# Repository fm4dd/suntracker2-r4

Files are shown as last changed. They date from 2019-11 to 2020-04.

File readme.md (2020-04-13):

# SunTracker2 Revision 4



This project is a photovoltaic (PV) solar tracking controller.

## Project

The design target is a self-orienting dual-axis, scheduled, Arduino-based solar
tracker model, demonstrating PV panel orientation for both Elevation and
Azimuth angles (dual-axis). The Sun orientation is achieved through pre-calculated
solar position data for a specific geographic location and time (scheduled).

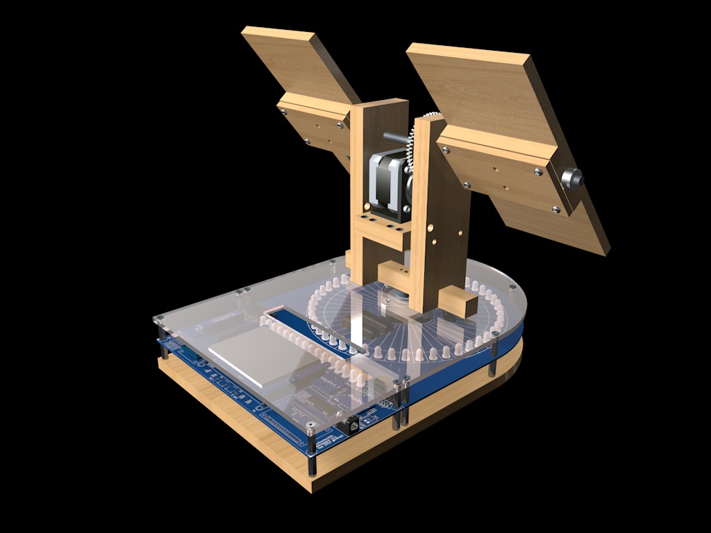
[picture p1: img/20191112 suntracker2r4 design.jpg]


Working under space, cost and time constraints, this prototype model is the
follow-up project to SunTracker2 Revision 3.

## Functional Design

In order to clearly understand, demonstrate and validate the sun tracking function,
a 48 dual-color LED ring represents the horizon with north, sunrise and sunset
indicators. A green indicator displays the suns daily movement over time.
Two NEMA stepper motors align the solar panel model with the sun.

### Board Components

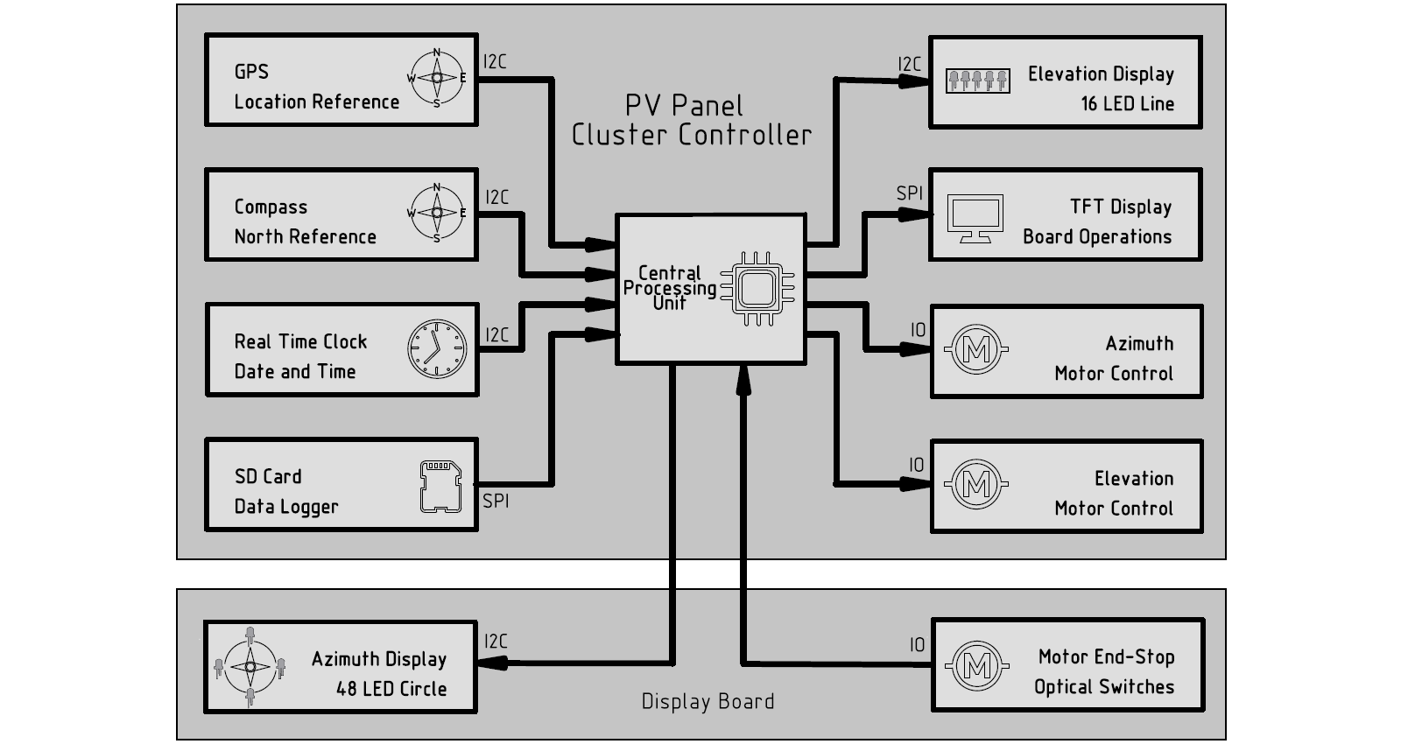
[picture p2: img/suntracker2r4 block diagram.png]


### Mainboard, PCB

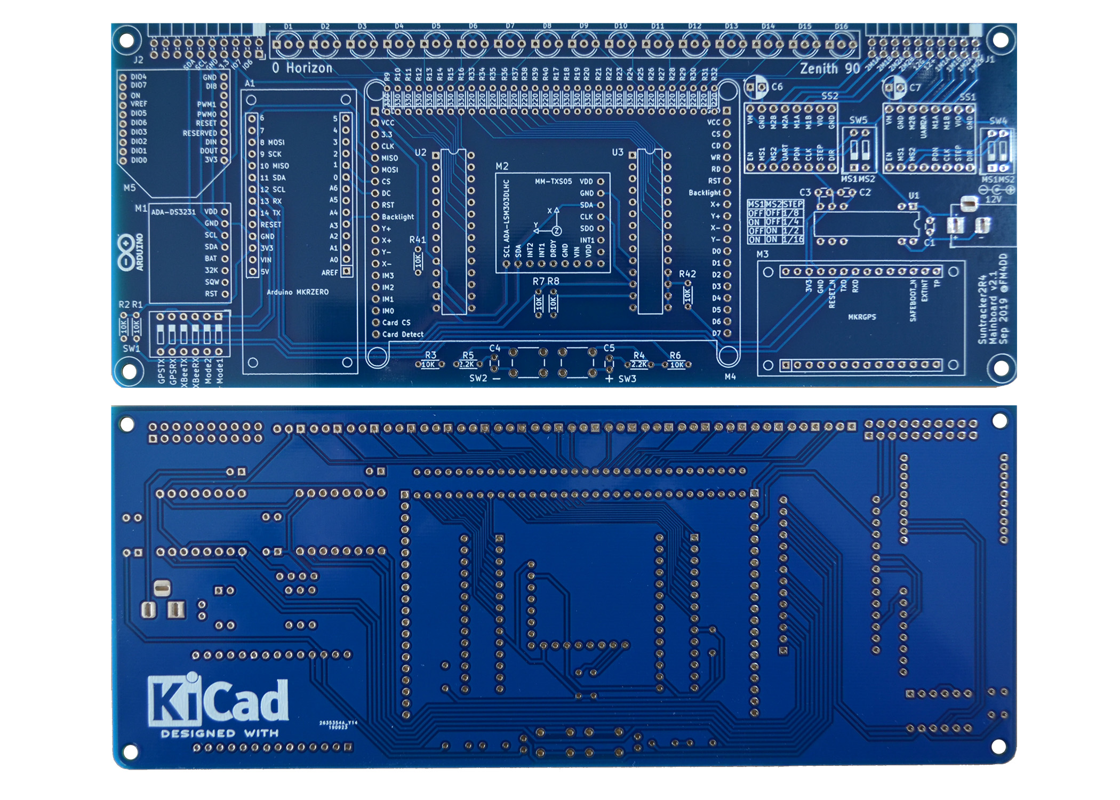
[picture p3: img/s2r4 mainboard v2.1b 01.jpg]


### Mainboard PCB, bottom layer 

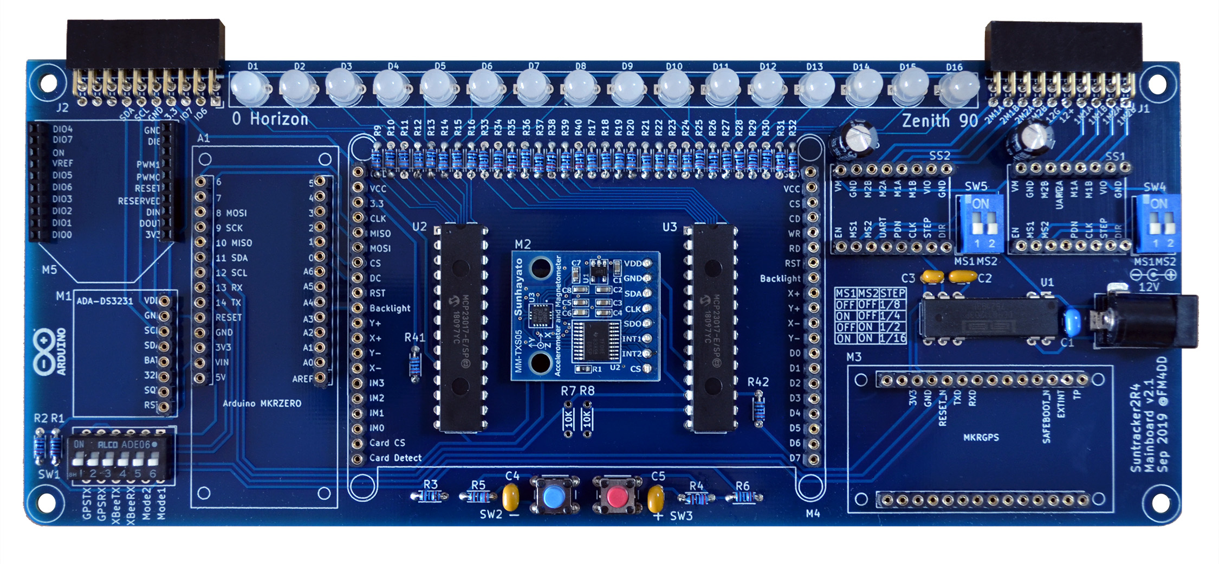
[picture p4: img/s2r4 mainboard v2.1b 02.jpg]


### Mainboard, fully populated

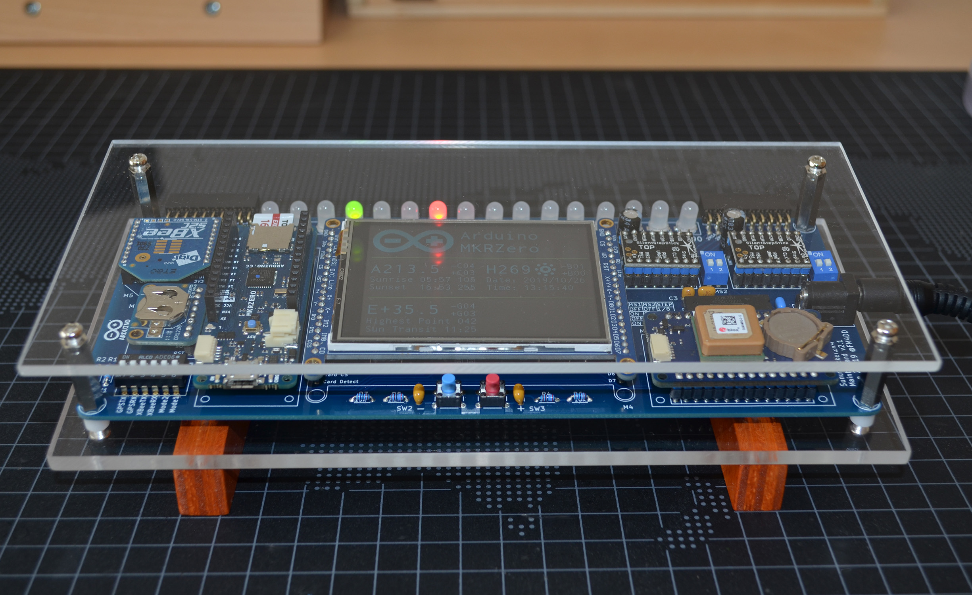
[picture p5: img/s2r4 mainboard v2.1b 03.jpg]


### Mainboard, TFT display layout

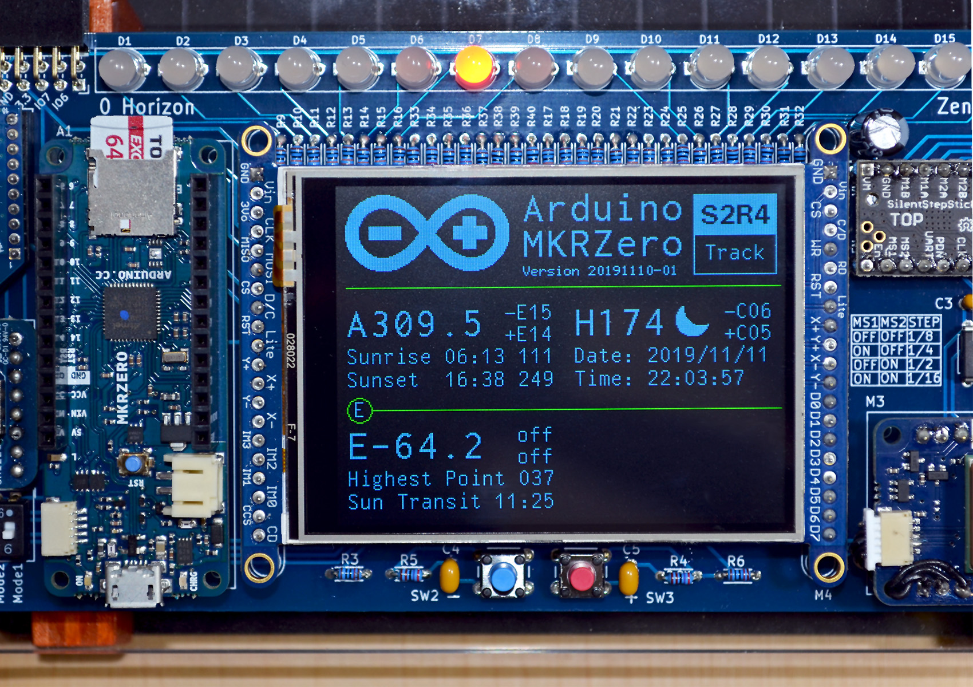
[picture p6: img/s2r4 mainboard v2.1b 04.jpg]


### Displayboard, PCB

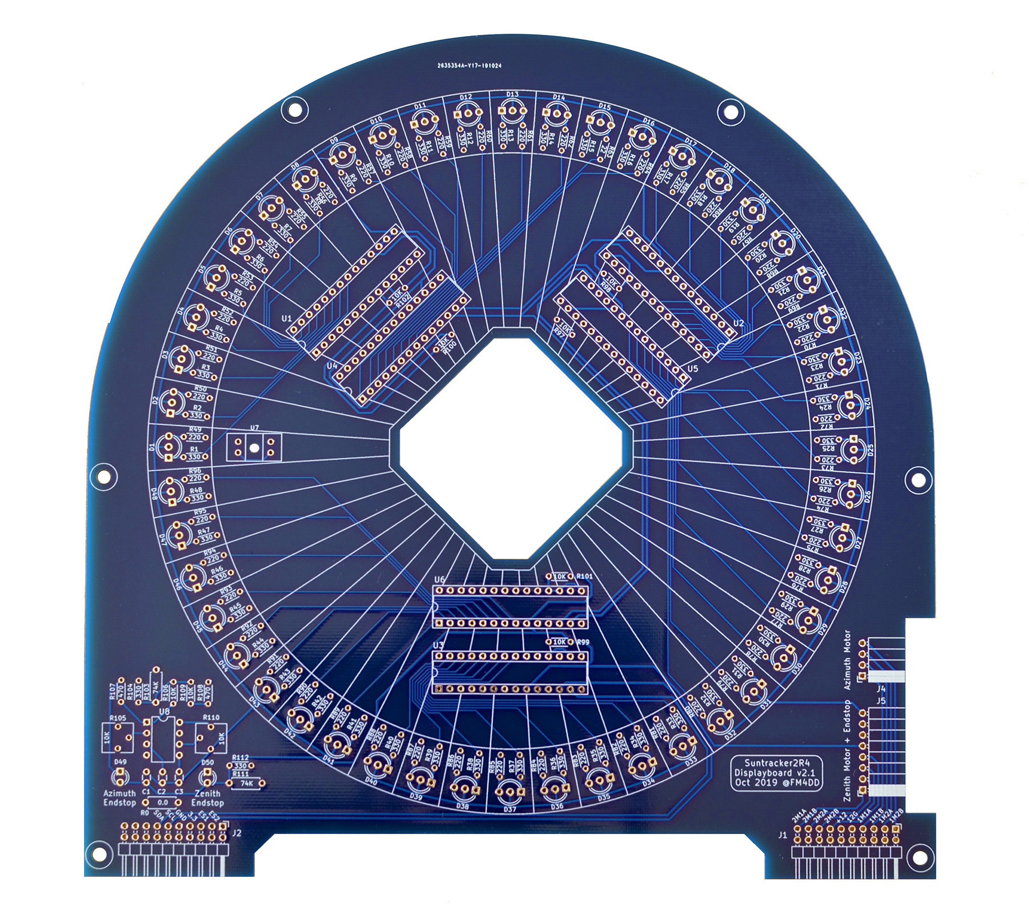
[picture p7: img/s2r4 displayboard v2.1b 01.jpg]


### Displayboard, IO Expander close-up

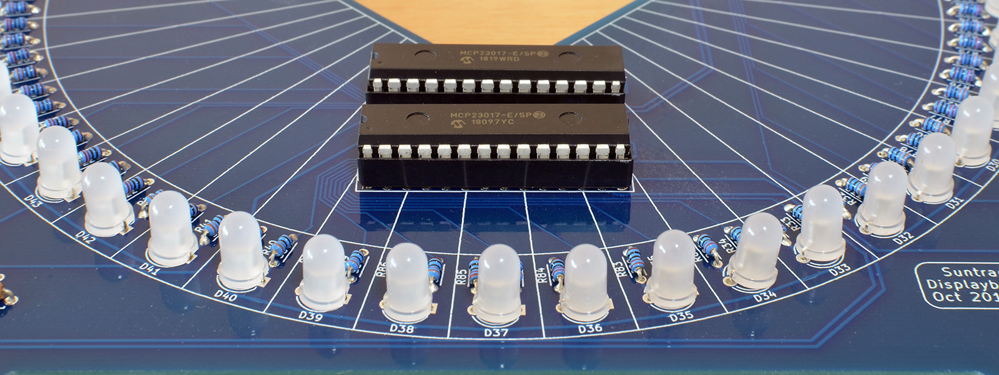
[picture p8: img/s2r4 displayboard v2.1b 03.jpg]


### Mainboard and Displayboard connected

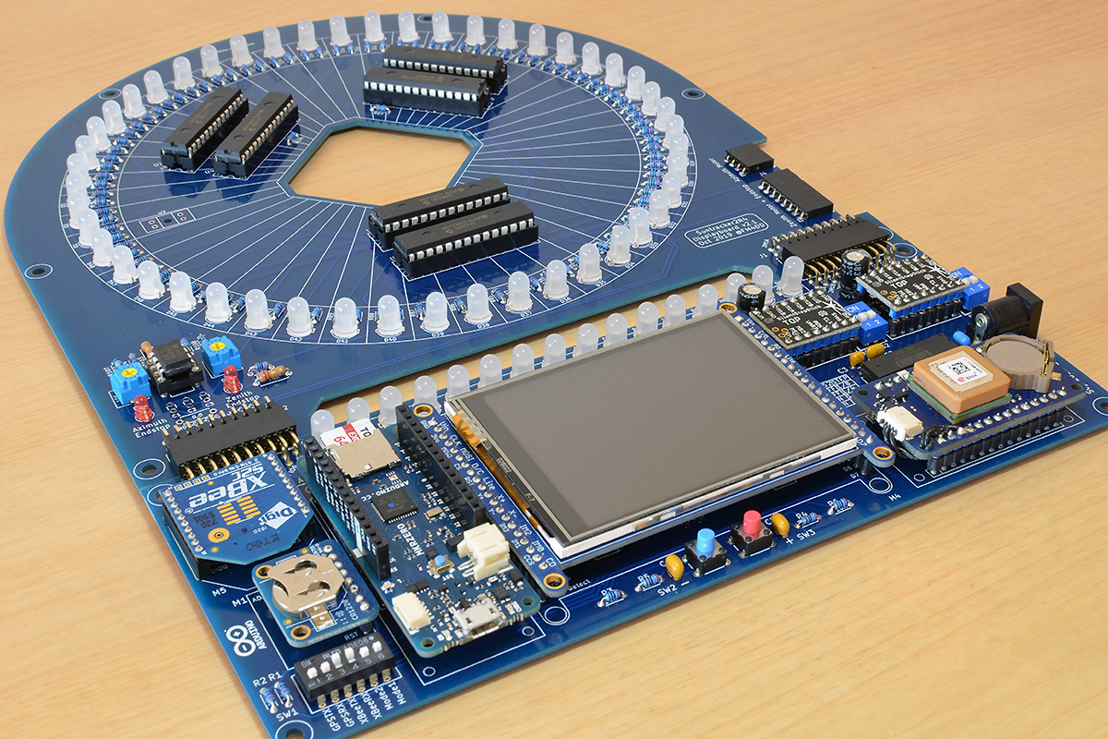
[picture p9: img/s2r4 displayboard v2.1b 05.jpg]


### Device Assembly

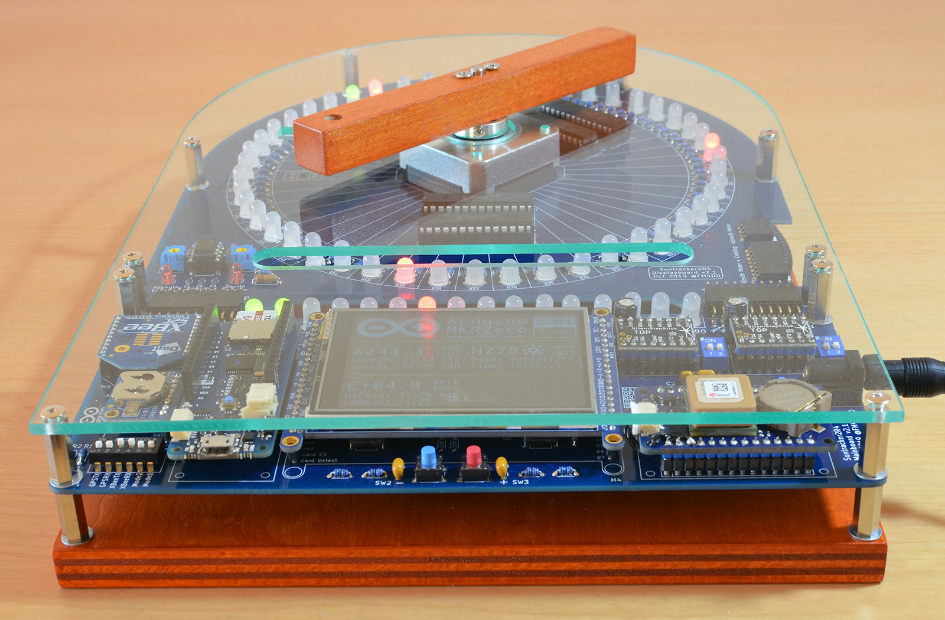
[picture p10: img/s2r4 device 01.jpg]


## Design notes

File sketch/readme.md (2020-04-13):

# mainboard-rev4 sketch compilation



```
Sketch uses 100056 bytes (38%) of program storage space. Maximum is 262144 bytes.
Global variables use 16600 bytes of dynamic memory.
Atmel SMART device 0x10010005 found
Device       : ATSAMD21G18A
Chip ID      : 10010005
Version      : v2.0 [Arduino:XYZ] Dec 20 2016 15:36:46
Address      : 8192
Pages        : 3968
Page Size    : 64 bytes
Total Size   : 248KB
Planes       : 1
Lock Regions : 16
Locked       : none
Security     : false
Boot Flash   : true
BOD          : true
BOR          : true
Arduino      : FAST_CHIP_ERASE
Arduino      : FAST_MULTI_PAGE_WRITE
Arduino      : CAN_CHECKSUM_MEMORY_BUFFER
Erase flash
done in 0.844 seconds

Write 100056 bytes to flash (1564 pages)

[=                             ] 4% (64/1564 pages)
[==                            ] 8% (128/1564 pages)
[===                           ] 12% (192/1564 pages)
[====                          ] 16% (256/1564 pages)
[======                        ] 20% (320/1564 pages)
[=======                       ] 24% (384/1564 pages)
[========                      ] 28% (448/1564 pages)
[=========                     ] 32% (512/1564 pages)
[===========                   ] 36% (576/1564 pages)
[============                  ] 40% (640/1564 pages)
[=============                 ] 45% (704/1564 pages)
[==============                ] 49% (768/1564 pages)
[===============               ] 53% (832/1564 pages)
[=================             ] 57% (896/1564 pages)
[==================            ] 61% (960/1564 pages)
[===================           ] 65% (1024/1564 pages)
[====================          ] 69% (1088/1564 pages)
[======================        ] 73% (1152/1564 pages)
[=======================       ] 77% (1216/1564 pages)
[========================      ] 81% (1280/1564 pages)
[=========================     ] 85% (1344/1564 pages)
[===========================   ] 90% (1408/1564 pages)
[============================  ] 94% (1472/1564 pages)
[============================= ] 98% (1536/1564 pages)
[==============================] 100% (1564/1564 pages)
done in 0.723 seconds

Verify 100056 bytes of flash with checksum.
Verify successful
done in 0.090 seconds
CPU reset.
```

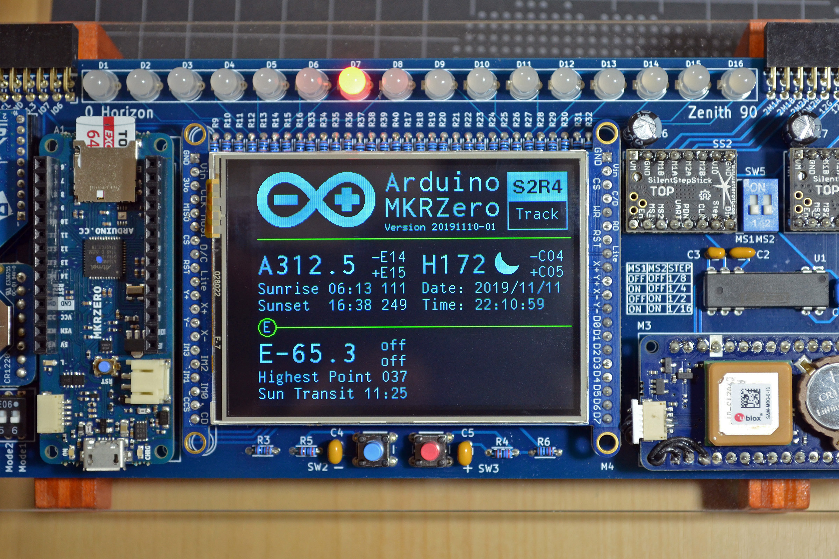
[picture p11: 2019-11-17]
img/s2r4 mainboard v2.1b 05.jpg

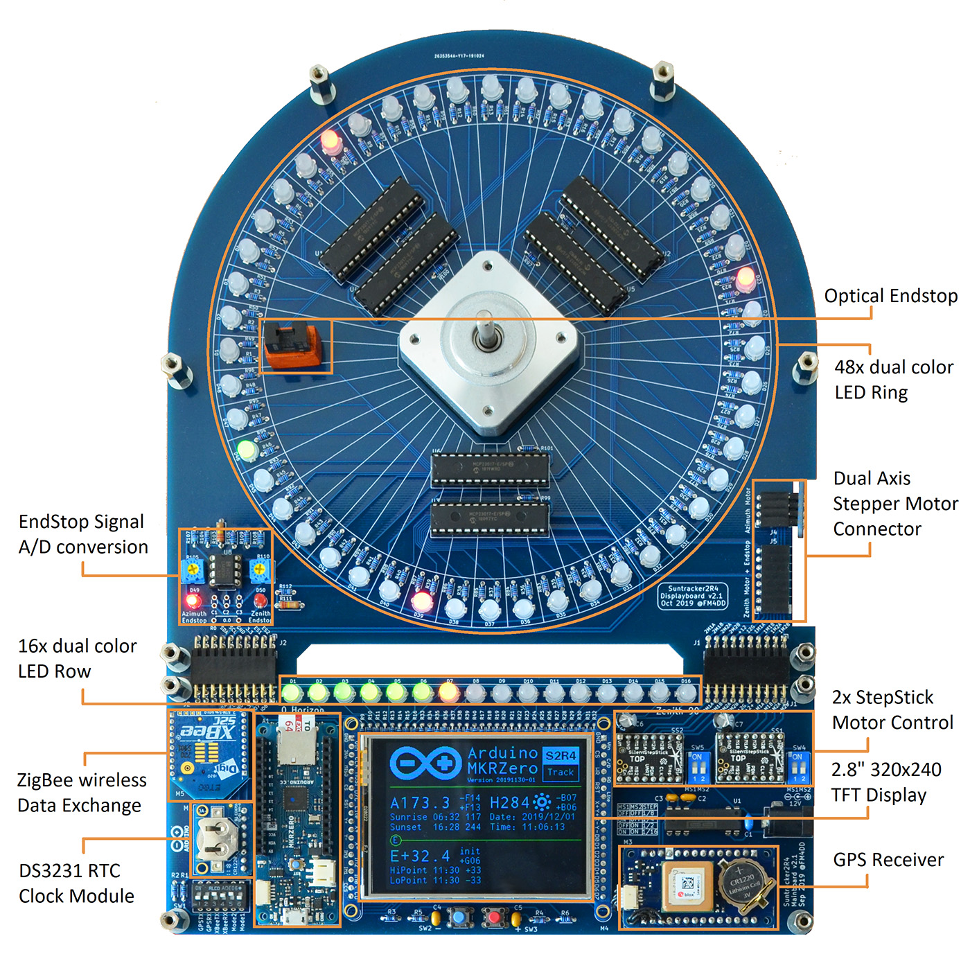
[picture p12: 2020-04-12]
img/s2r4 description.jpg

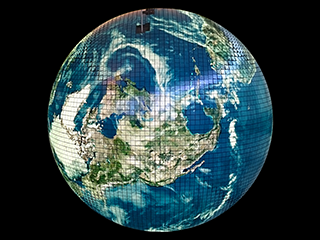
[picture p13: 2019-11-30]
sketch/mainboard-rev4/s2r4img.bmp

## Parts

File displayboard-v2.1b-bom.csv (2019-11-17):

Manufacturer Part Number | Manufacturer | Digi-Key Part Number | Customer Reference | Quantity | Description
K104K15X7RF5TL2 | Vishay BC Components | BC1084CT-ND | C1,C2,C3 | 3 | CAP CER 0.1UF 50V X7R RADIAL
CD14ZT0R00 | Stackpole Electronics Inc | CD14ZT0R00CT-ND | R0 | 1 | RES 0 OHM 1/4W JUMP AXIAL
RNMF14FTC330R | Stackpole Electronics Inc | S330CACT-ND | R1-48,R104,R112 | 50 | RES 330 OHM 1/4W 1% AXIAL
RNMF14FTC470R | Stackpole Electronics Inc | S470CACT-ND | R107,R108 | 2 | RES 470 OHM 1/4W 1% AXIAL
RNMF14FTC220R | Stackpole Electronics Inc | S220CACT-ND | R49-96 | 48 | RES 220 OHM 1/4W 1% AXIAL
RNMF14FTC10K0 | Stackpole Electronics Inc | S10KCACT-ND | R97-R102 | 6 | RES 10K OHM 1/4W 1% AXIAL
PEC10DBAN | Sullins Connector Solutions | S2112E-10-ND | J1,J2 | 2 | CONN HEADER R/A 20POS 2.54MM
PPPC041LGBN-RC | Sullins Connector Solutions | S5479-ND | J4 | 1 | CONN HDR 4POS 0.1 GOLD PCB R/A
PPPC081LGBN-RC | Sullins Connector Solutions | S5483-ND | J5 | 1 | CONN HDR 8POS 0.1 GOLD PCB R/A
ROB-09238 | SparkFun Electronics | 1568-1105-ND | M1,M2 | 2 | STEPPER MOTOR HYBRID BIPOLAR 12V
LTL-30EHJ | Lite-On Inc. | 160-1057-ND | D1-D48 | 48 | LED GRN/RED DIFFUSED T-1 3/4 T/H
151031SS04000 | Wurth Electronics Inc. | 732-5005-ND | D49,D50 | 2 | LED RED DIFFUSED 3MM ROUND T/H
ED281DT | On Shore Technology Inc. | ED3050-5-ND | U1-U6 | 6 | CONN IC DIP SOCKET 28POS TIN
MCP23017-E/SP | Microchip Technology | MCP23017-E/SP-ND | U1-U6 | 6 | IC I/O EXPANDER I2C 16B 28SDIP
OPB804 | TT Electronics/Optek Technology | 365-1017-ND | U7,U9 | 2 | OPB804 SENSOR OPT SLOT PHOTOTRAN PCB MT
LM393P | Texas Instruments | 296-1398-5-ND | U8 | 1 | LM393 IC DUAL DIFF COMP 8-DIP

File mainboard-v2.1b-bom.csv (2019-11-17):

Manufacturer Part Number | Manufacturer | Digi-Key Part Number | Customer Reference | Quantity | Description
ABX00012 | Arduino | 1050-1137-ND | A1 | 1 | ARDUINO MKR ZERO W/ HDR ATSAMD21
ASX00017 | Arduino | 1050-1171-ND | M3 | 1 | ARDUINO MKR GPS SHIELD
MCP23017-E/SP | Microchip Technology | MCP23017-E/SP-ND | U1,U2 | 2 | IC I/O EXPANDER I2C 16B 28SDIP
1770 | Adafruit Industries LLC | 1528-1469-ND | M4 | 1 | 2.8" TFT LCD TOUCHSCREEN
1120 | Adafruit Industries LLC | 1528-1173-ND | M2 | 1 | BOARD ACCEL/COMPASS 3AXIS LSM303
3013 | Adafruit Industries LLC | 1528-1598-ND | M1 | 1 | ADAFRUIT DS3231 PRECISION RTC BR
TMC2208 SILENTSTEPSTICK | Trinamic Motion Control GmbH | 1460-1201-ND | SS1,SS2 | 2 | TMC2208 STEPPER DRIVER BOARD
1825057-1 | TE Connectivity ALCOSWITCH Switches | 450-1363-ND | SWI4,SWI5 | 2 | SWITCH SLIDE DIP SPST 100MA 24V
1825360-4 | TE Connectivity ALCOSWITCH Switches | 450-3353-ND | SWI1 | 1 | SWITCH SLIDE DIP SPST 100MA 24V
151031SS04000 | Wurth Electronics Inc. | 732-5005-ND | D1,D2,D3,D4 | 4 | LED RED DIFFUSED 3MM ROUND T/H
C320C105K5N5TA91707301 | KEMET | 399-14394-1-ND | C1,C2 | 2 | CAP CER 1UF 50V X8L RADIAL
DCR011203P | Texas Instruments | 296-36927-5-ND | U1 | 1 | DC DC CONVERTER 3.3V 1W
476CKE035M | Illinois Capacitor | 1572-1473-ND | C6,C7 | 2 | CAP ALUM 47UF 20% 35V RADIAL
PPTC102LJBN-RC | Sullins Connector Solutions | S5524-ND | J1,J2 | 2 | CONN HDR 20POS 0.1 TIN PCB R/A
SMC-1-40-1-GT | Adam Tech | 2057-SMC-1-40-1-GT-ND | Circuit Sockets | 2 | MACHINE PIN SOCKET 40P 1.00MM PI
1825910-6 | TE Connectivity ALCOSWITCH Switches | 450-1650-ND | SWI2,SWI3 | 2 | SWITCH TACTILE SPST-NO 0.05A 24V
RNMF14FTC10K0 | Stackpole Electronics Inc | S10KCACT-ND | R1,R2,R5,R6,R9,R10,R11,R12,R13,R14 | 10 | RES 10K OHM 1/4W 1% AXIAL
RNMF14FTC330R | Stackpole Electronics Inc | S330CACT-ND | R3,R4,R7,R8 | 16 | RES 330 OHM 1/4W 1% AXIAL
RNMF14FTC220R | Stackpole Electronics Inc | S220CACT-ND | R3,R4,R7,R8 | 16 | RES 220 OHM 1/4W 1% AXIAL
RNMF14FTC2K20 | Stackpole Electronics Inc | S2.2KCACT-ND | R15,R16 | 2 | RES 2.2K OHM 1/4W 1% AXIAL
PJ-002A | CUI Inc. | CP-002A-ND | 12V Barrel Jack | 1 | CONN PWR JACK 2X5.5MM SOLDER
LTL-30EHJ | Lite-On Inc. | 160-1057-ND | D1-D16 | 16 | LED GRN/RED DIFFUSED T-1 3/4 T/H
XB24CZ7PIT-004 | Digi International | 602-1557-ND | M5 | 1 | RF TXRX MOD 802.15.4 TRACE ANT

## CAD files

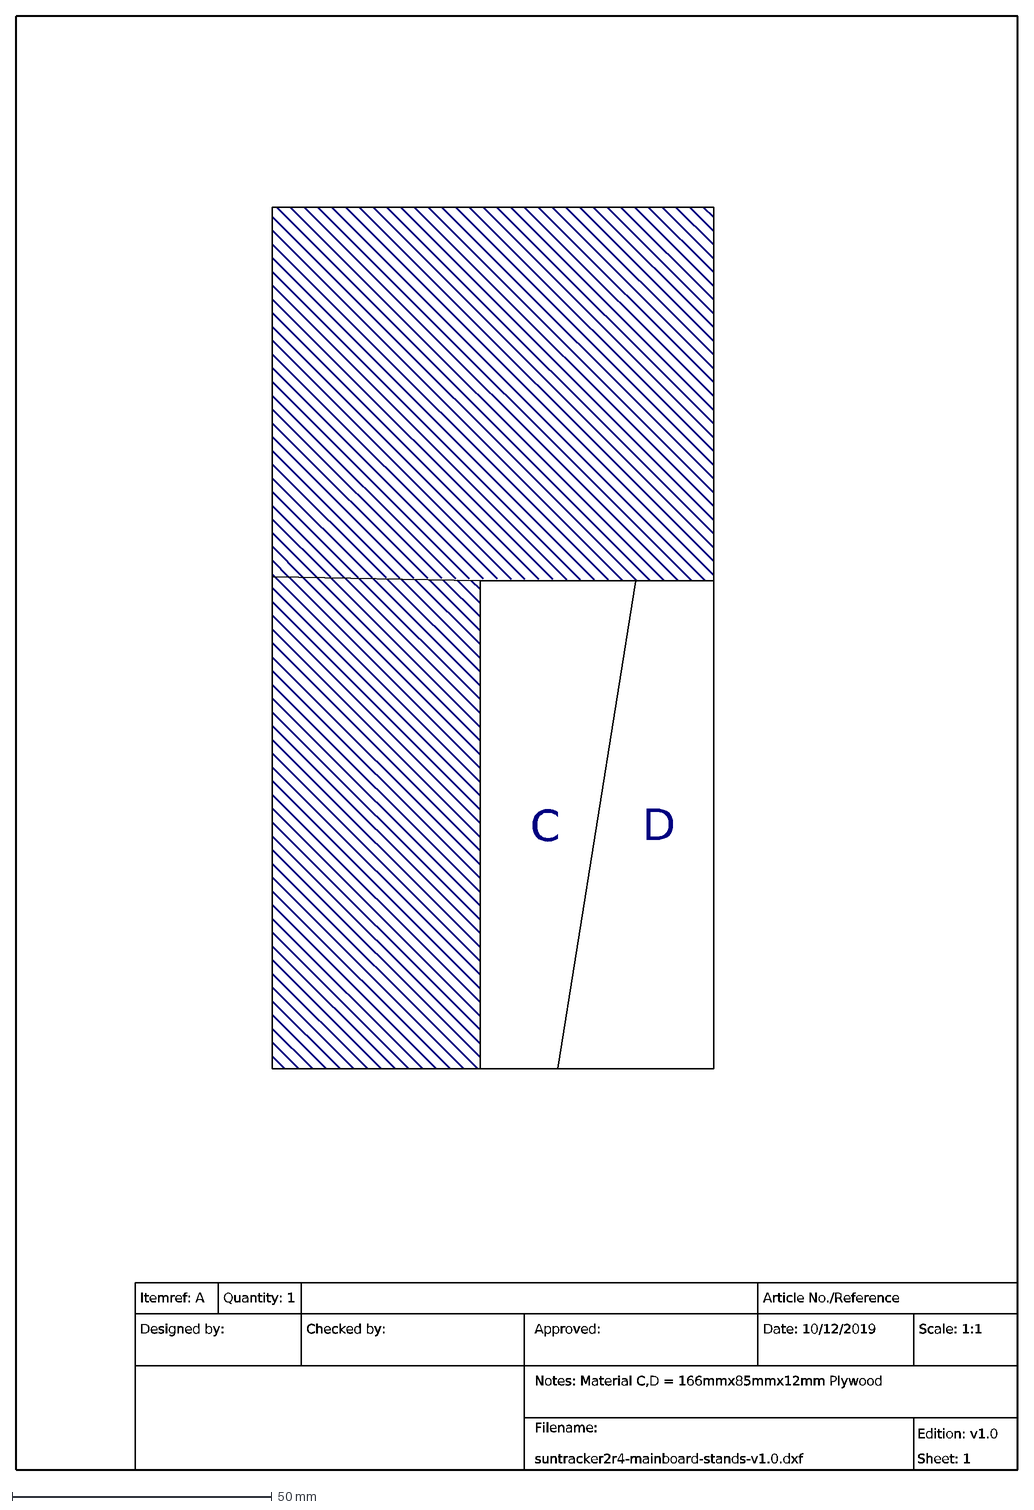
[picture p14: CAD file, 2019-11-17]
cad/20191012 suntracker2r4-mainboard-stands-v1.0.dxf
Notes: Material C,D = 166mmx85mmx12mm Plywood
Itemref: A
Quantity: 1
Article No./Reference
Designed by:
Checked by:
Approved:
Filename: suntracker2r4-mainboard-stands-v1.0.dxf
Date: 10/12/2019
Scale: 1:1
Edition: v1.0 Sheet: 1
C
D

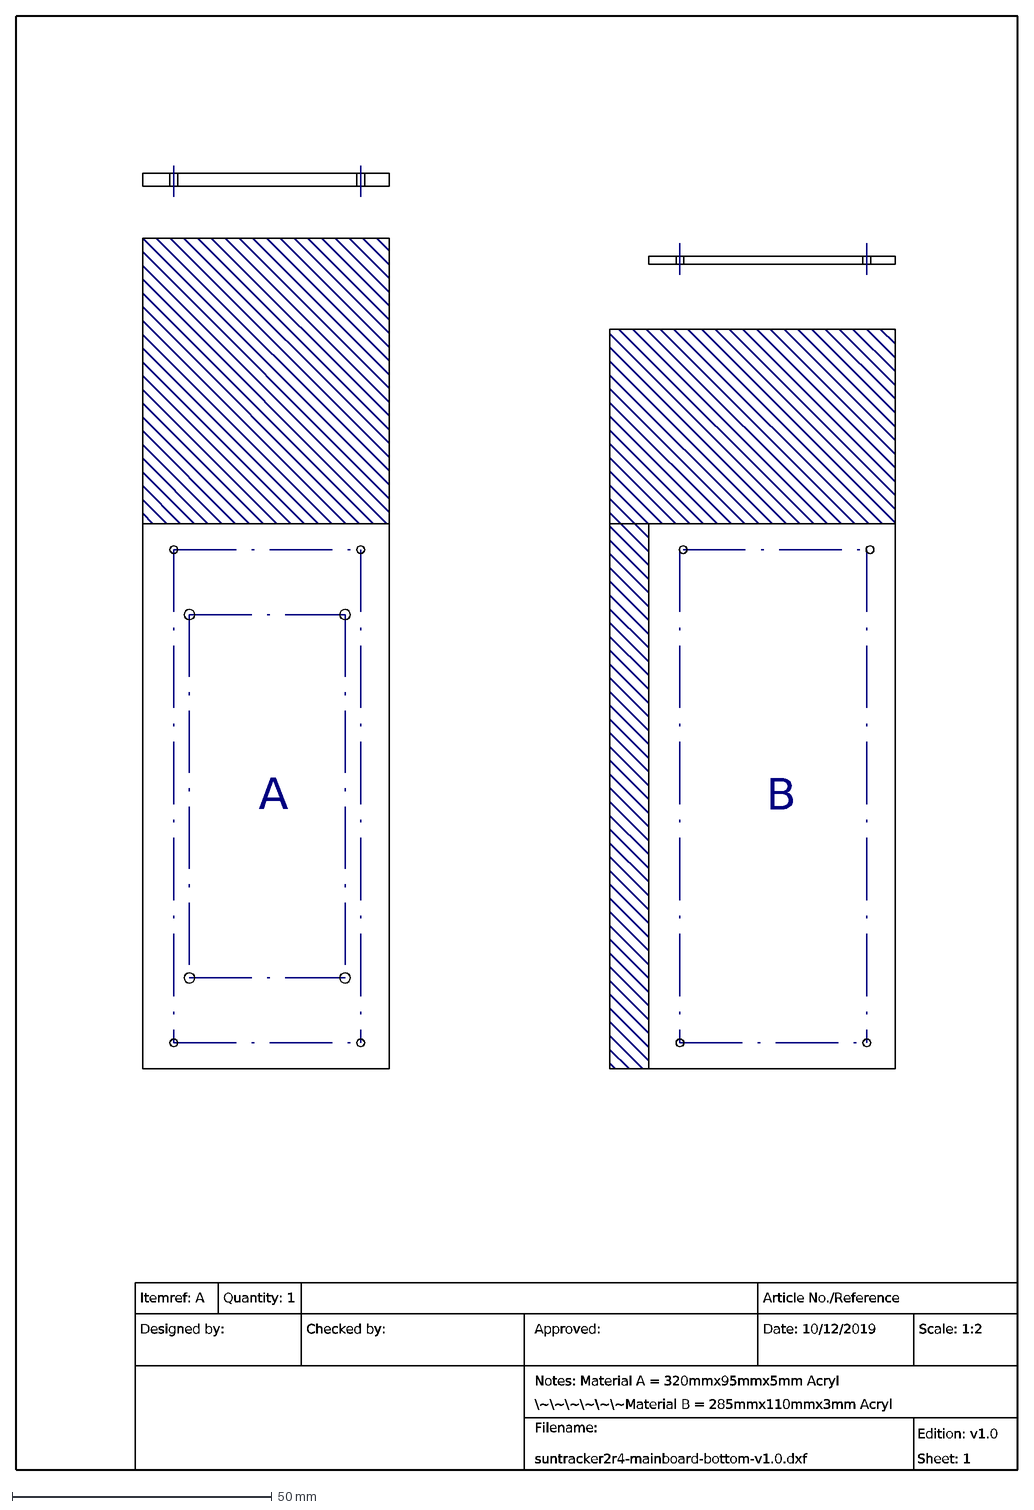
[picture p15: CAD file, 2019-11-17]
cad/20191012 suntracker2r4-mainboard-bottom-v1.0.dxf
Notes: Material A = 320mmx95mmx5mm Acryl \~\~\~\~\~\~Material B = 285mmx110mmx3mm Acryl
Itemref: A
Quantity: 1
Article No./Reference
Designed by:
Checked by:
Approved:
Filename: suntracker2r4-mainboard-bottom-v1.0.dxf
Date: 10/12/2019
Scale: 1:2
Edition: v1.0 Sheet: 1
A
B

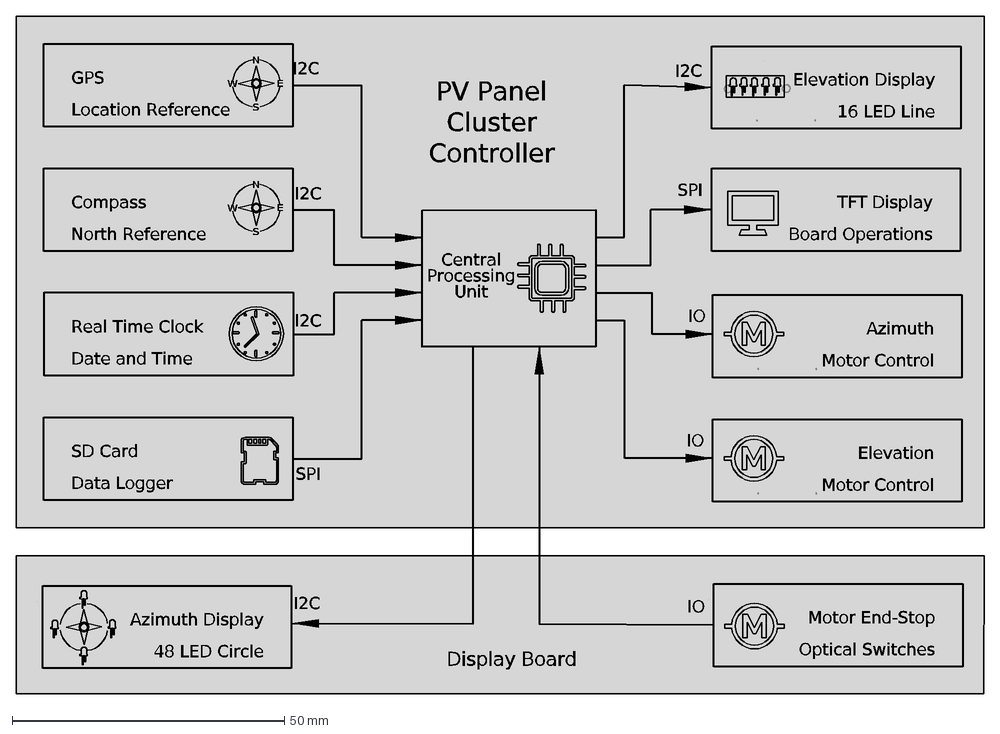
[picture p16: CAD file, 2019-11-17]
cad/20190922 Suntracker2r4 block diagram.dxf
Compass North Reference
GPS Location Reference
Real Time Clock Date and Time
Azimuth Display 48 LED Circle
Motor End-Stop Optical Switches
Elevation Display 16 LED Line
TFT Display Board Operations
SD Card Data Logger
Azimuth Motor Control
Elevation Motor Control
Central Processing Unit
S
W
E
N
SPI
I2C
IO
Display Board
PV Panel Cluster Controller

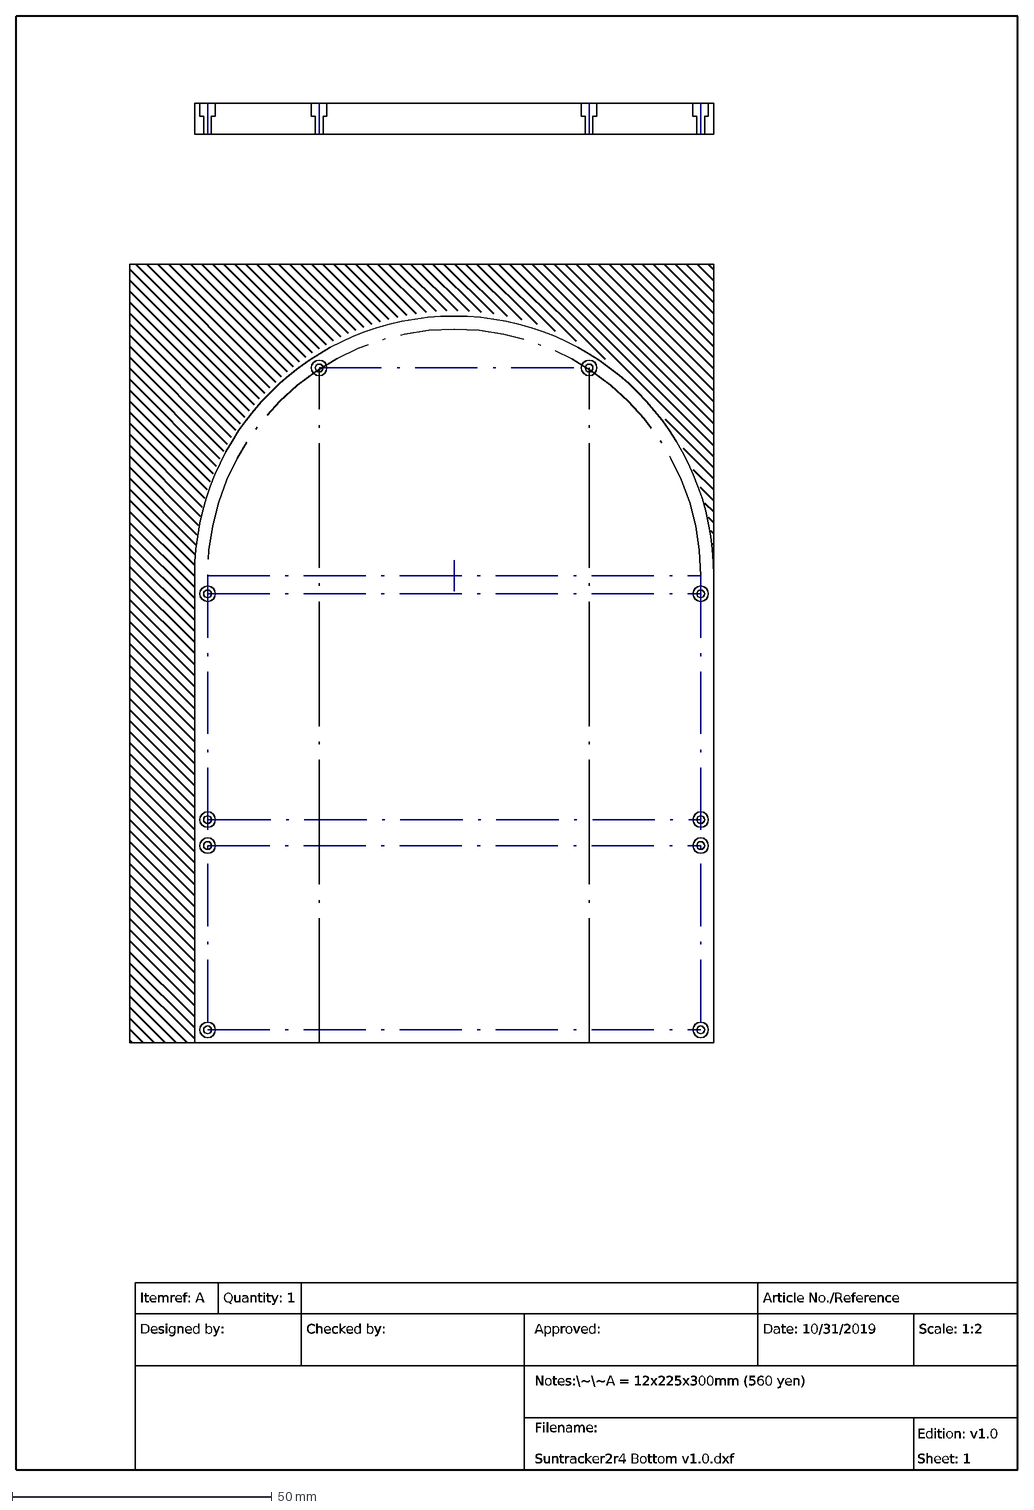
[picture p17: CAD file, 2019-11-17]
cad/20191031 Suntracker2r4 enclosure Bottom v1.0.dxf
Notes:\~\~A = 12x225x300mm (560 yen)
Itemref: A
Quantity: 1
Article No./Reference
Designed by:
Checked by:
Approved:
Filename: Suntracker2r4 Bottom v1.0.dxf
Date: 10/31/2019
Scale: 1:2
Edition: v1.0 Sheet: 1

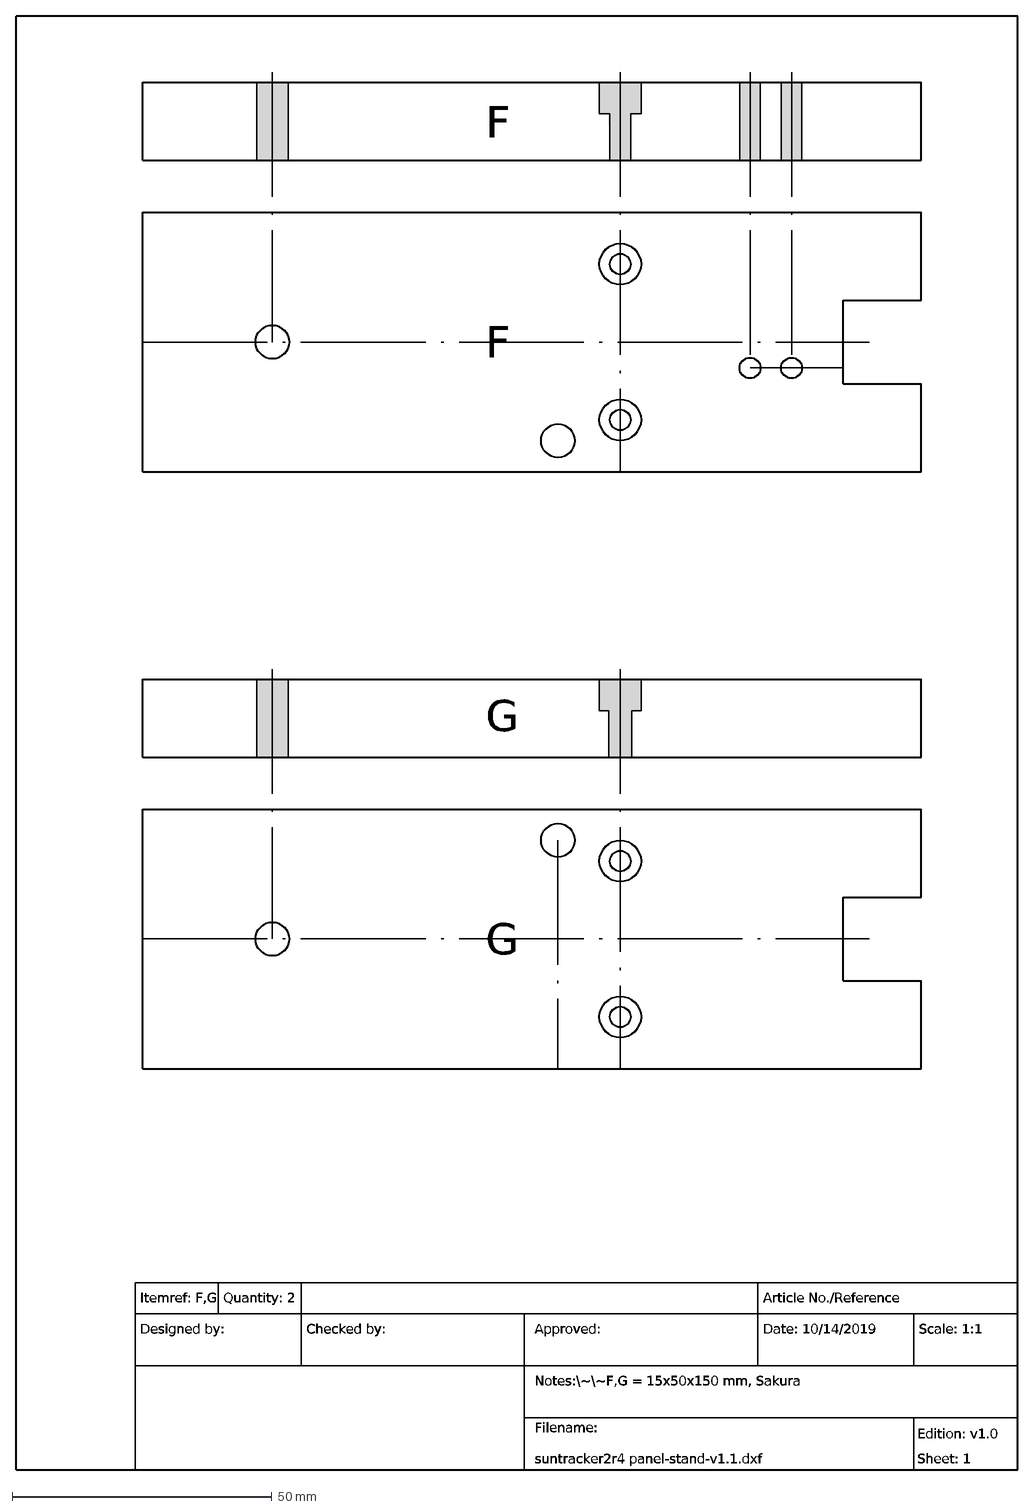
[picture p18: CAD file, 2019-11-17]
cad/20191014 Suntracker2r4 panel-stand-v1.1.dxf
Notes:\~\~F,G = 15x50x150 mm, Sakura
Itemref: F,G
F
G
Quantity: 2
Article No./Reference
Designed by:
Checked by:
Approved:
Filename: suntracker2r4 panel-stand-v1.1.dxf
Date: 10/14/2019
Scale: 1:1
Edition: v1.0 Sheet: 1

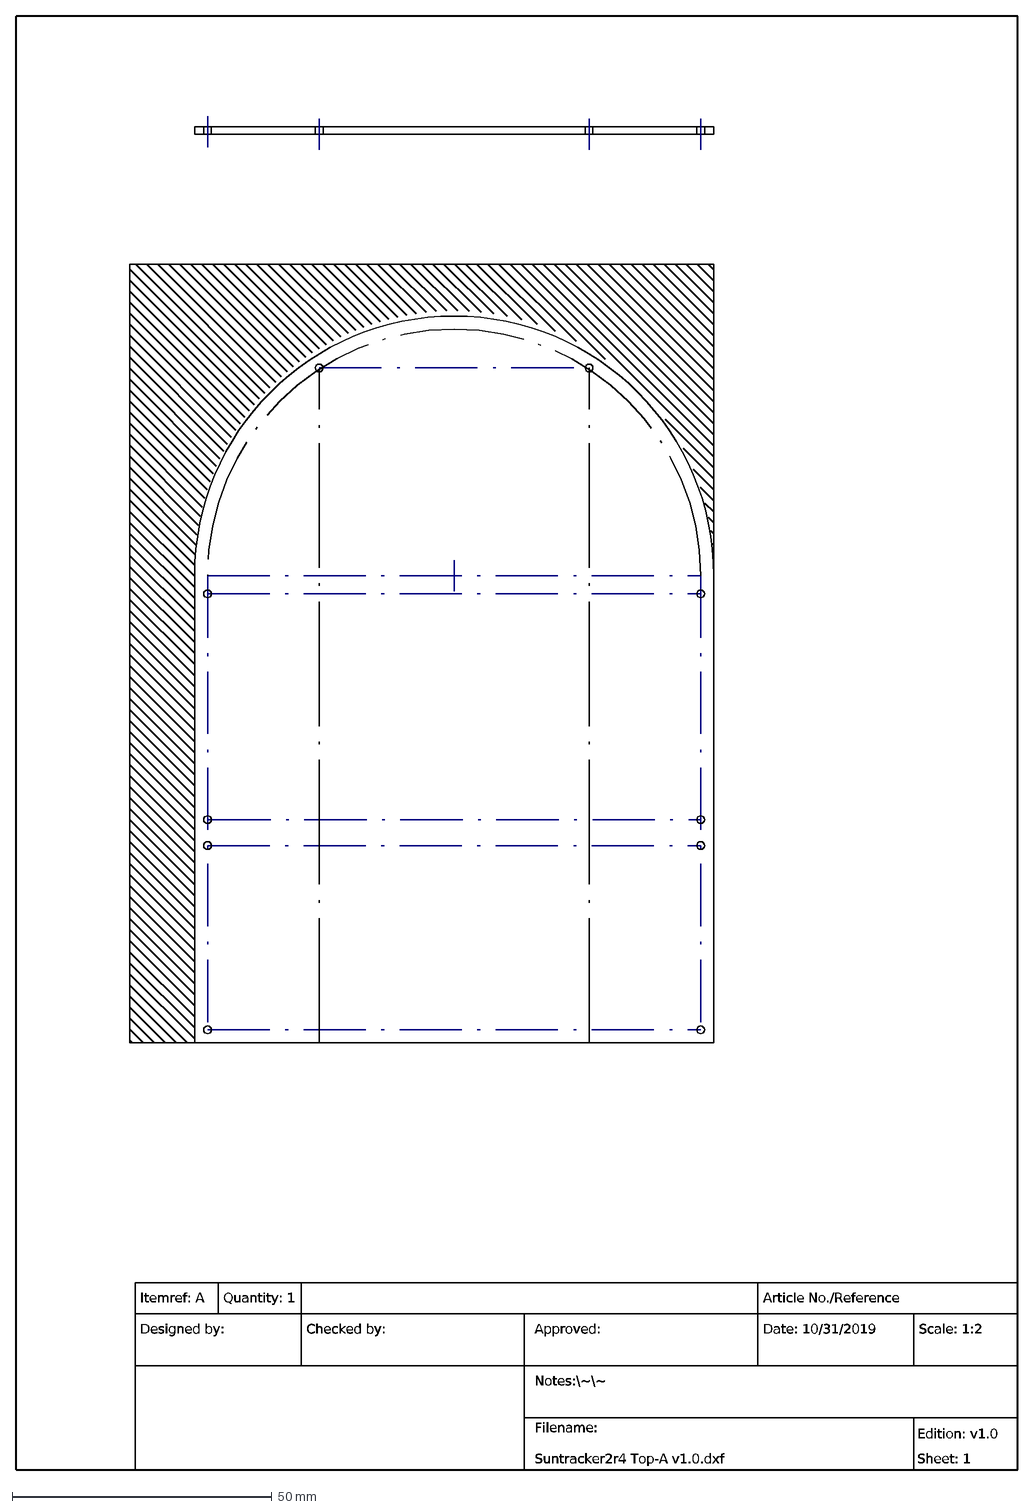
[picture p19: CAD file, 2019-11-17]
cad/20191031 Suntracker2r4 enclosure TopA v1.0.dxf
Notes:\~\~
Itemref: A
Quantity: 1
Article No./Reference
Designed by:
Checked by:
Approved:
Filename: Suntracker2r4 Top-A v1.0.dxf
Date: 10/31/2019
Scale: 1:2
Edition: v1.0 Sheet: 1

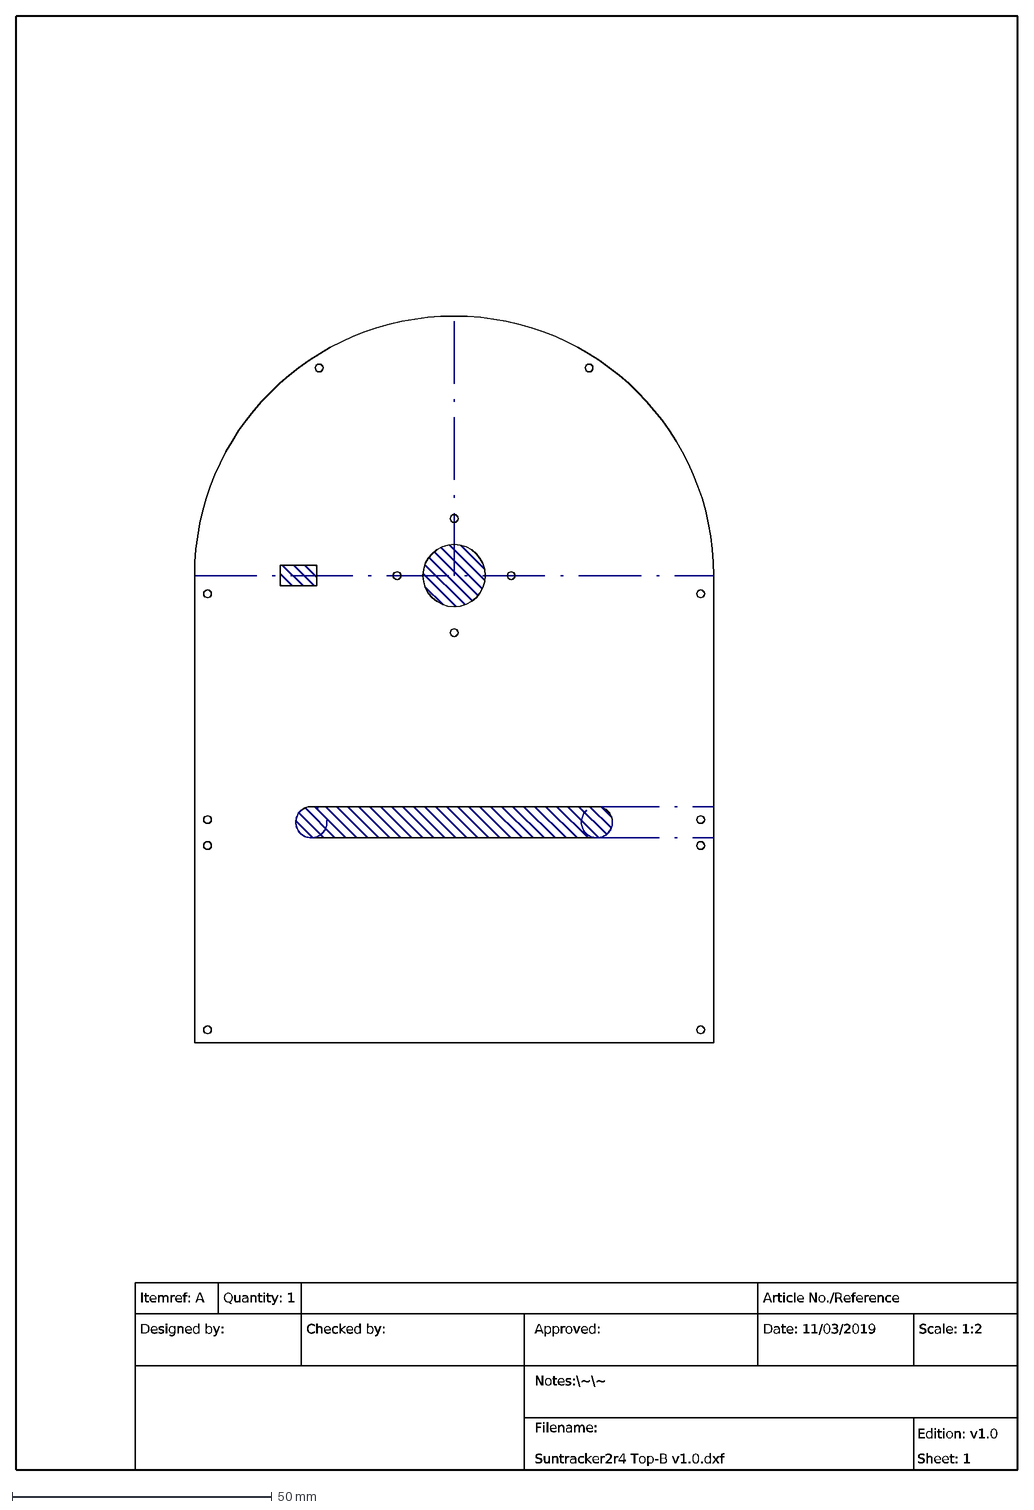
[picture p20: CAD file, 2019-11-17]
cad/20191031 Suntracker2r4 enclosure TopB v1.0.dxf
Notes:\~\~
Itemref: A
Quantity: 1
Article No./Reference
Designed by:
Checked by:
Approved:
Filename: Suntracker2r4 Top-B v1.0.dxf
Date: 11/03/2019
Scale: 1:2
Edition: v1.0 Sheet: 1

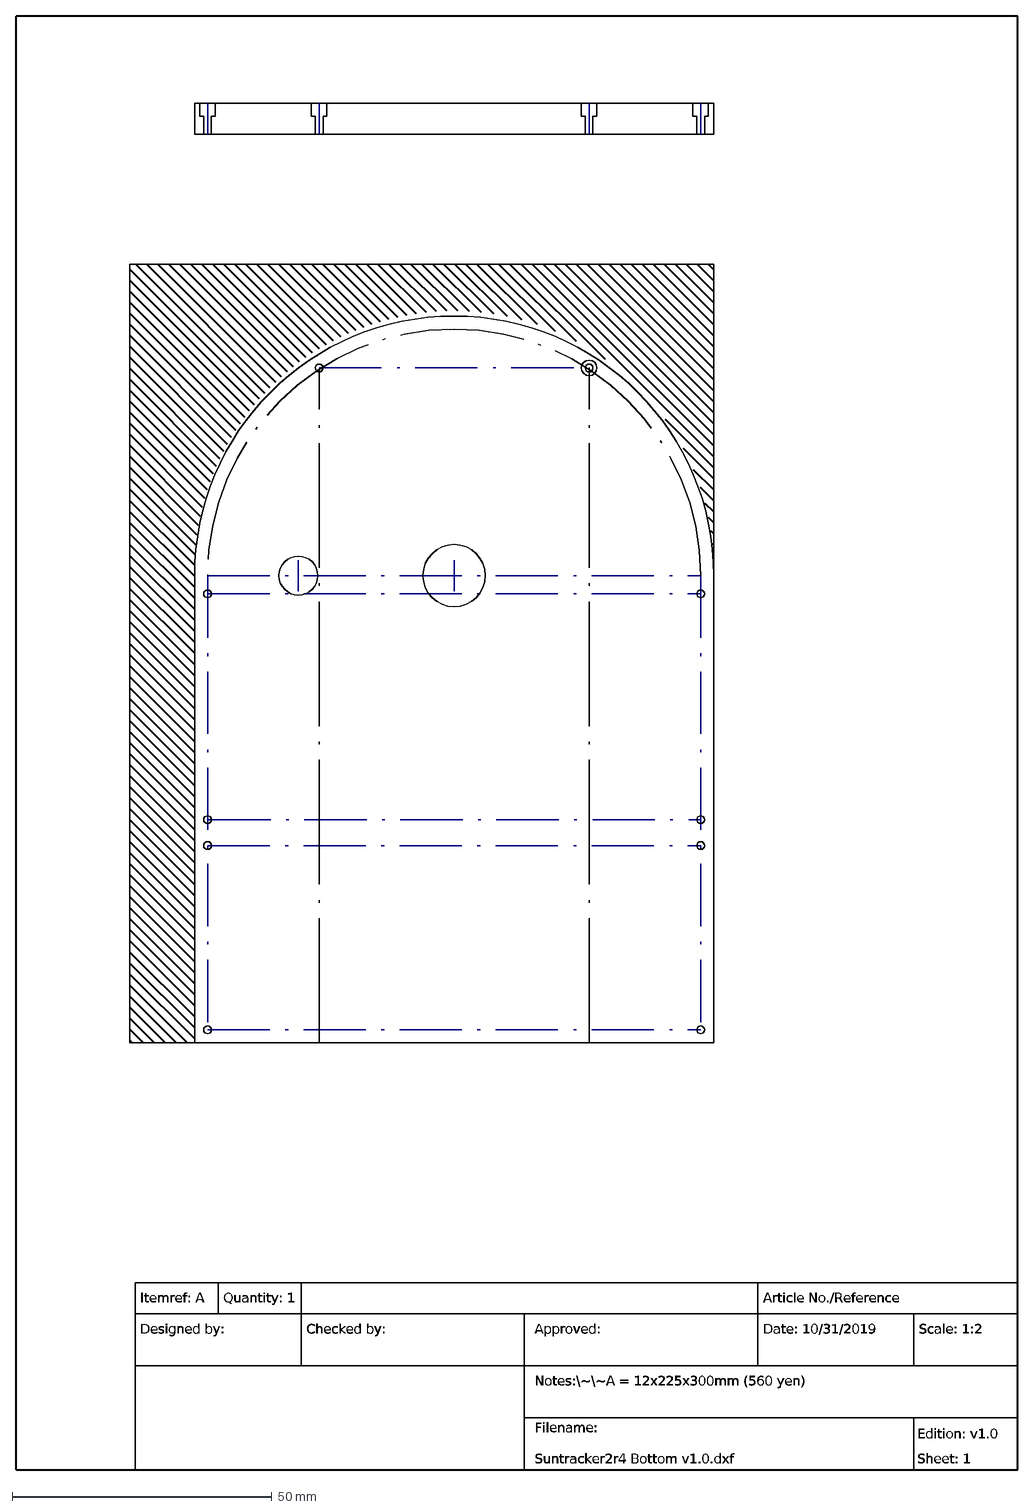
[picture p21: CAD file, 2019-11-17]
cad/20191031 Suntracker2r4 enclosure Top v1.0.dxf
Notes:\~\~A = 12x225x300mm (560 yen)
Itemref: A
Quantity: 1
Article No./Reference
Designed by:
Checked by:
Approved:
Filename: Suntracker2r4 Bottom v1.0.dxf
Date: 10/31/2019
Scale: 1:2
Edition: v1.0 Sheet: 1

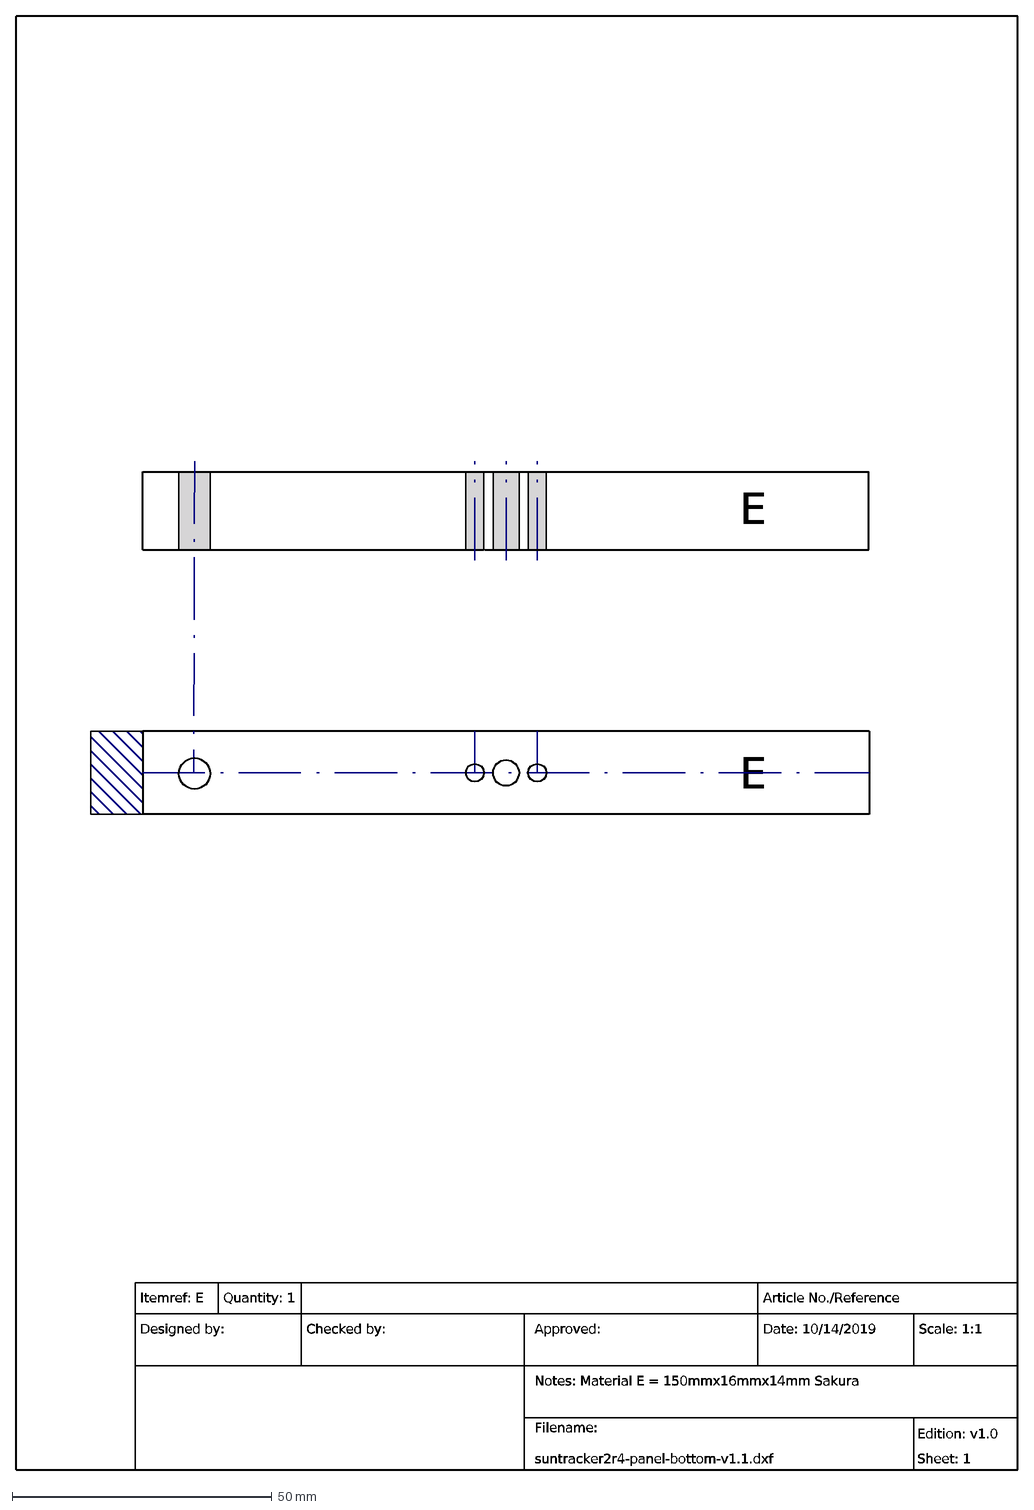
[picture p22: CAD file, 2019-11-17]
cad/20191014 suntracker2r4-panel-bottom-v1.1.dxf
Notes: Material E = 150mmx16mmx14mm Sakura
Itemref: E
Quantity: 1
Article No./Reference
Designed by:
Checked by:
Approved:
E
Filename: suntracker2r4-panel-bottom-v1.1.dxf
Date: 10/14/2019
Scale: 1:1
Edition: v1.0 Sheet: 1

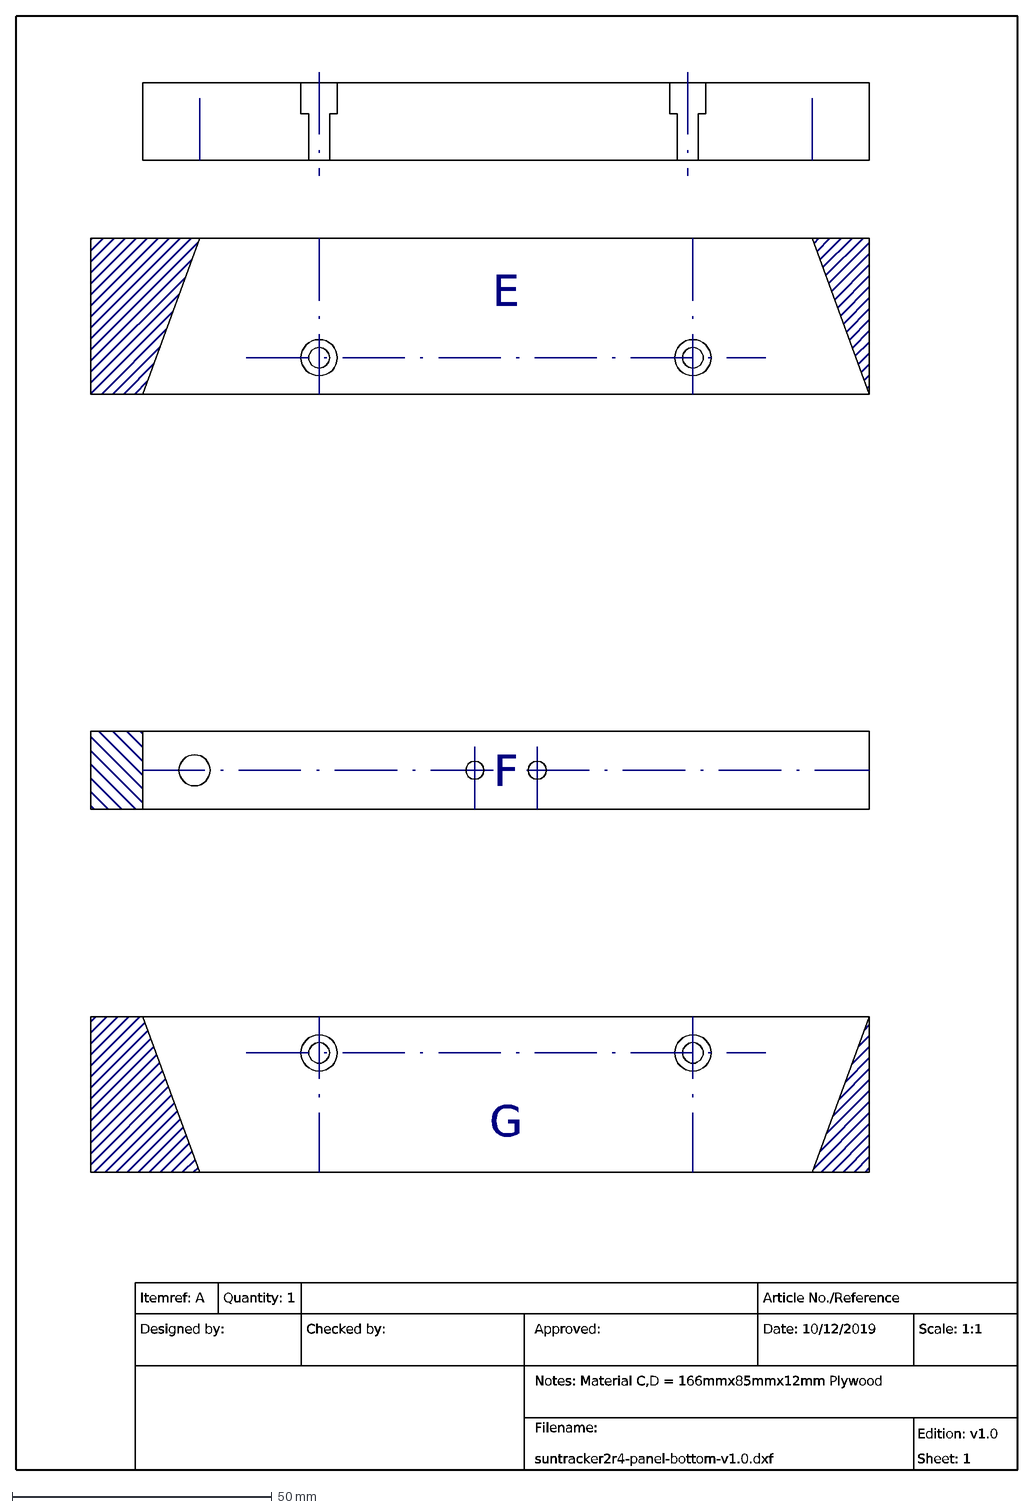
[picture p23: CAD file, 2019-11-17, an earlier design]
cad/20191014 suntracker2r4-panel-bottom-v1.0.dxf
Notes: Material C,D = 166mmx85mmx12mm Plywood
Itemref: A
Quantity: 1
Article No./Reference
Designed by:
Checked by:
Approved:
Filename: suntracker2r4-panel-bottom-v1.0.dxf
Date: 10/12/2019
Scale: 1:1
Edition: v1.0 Sheet: 1
E
G
F

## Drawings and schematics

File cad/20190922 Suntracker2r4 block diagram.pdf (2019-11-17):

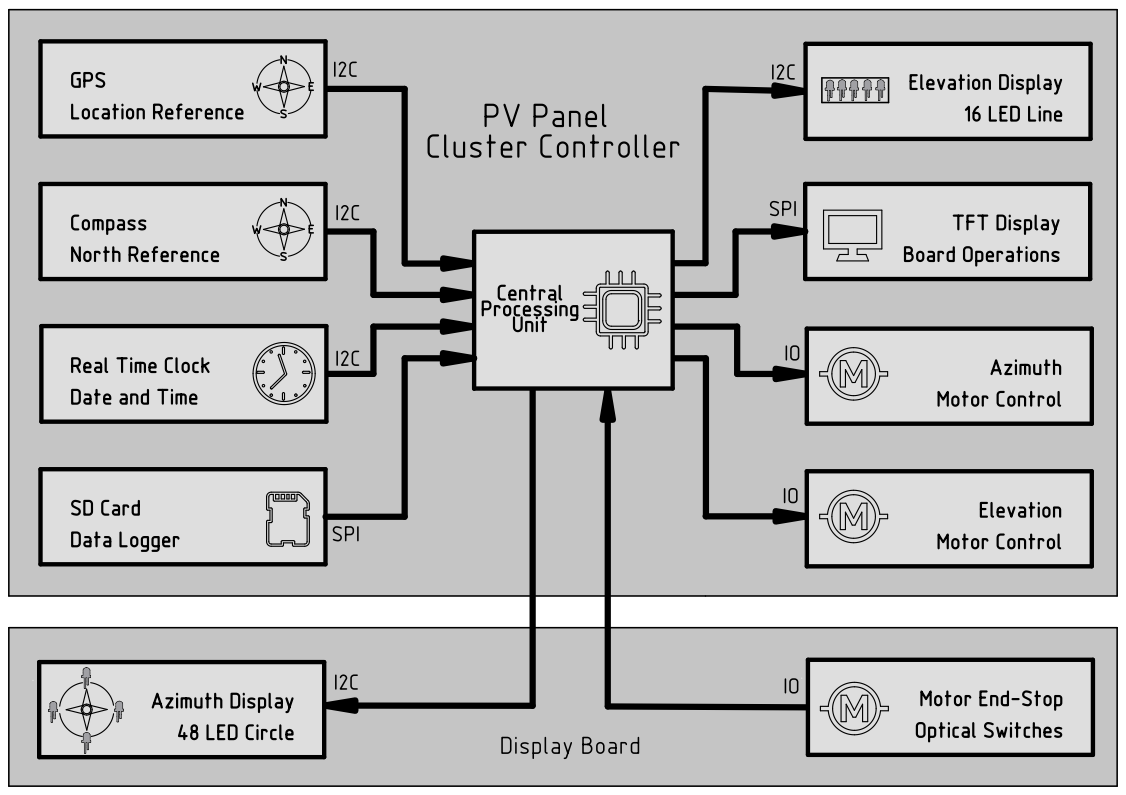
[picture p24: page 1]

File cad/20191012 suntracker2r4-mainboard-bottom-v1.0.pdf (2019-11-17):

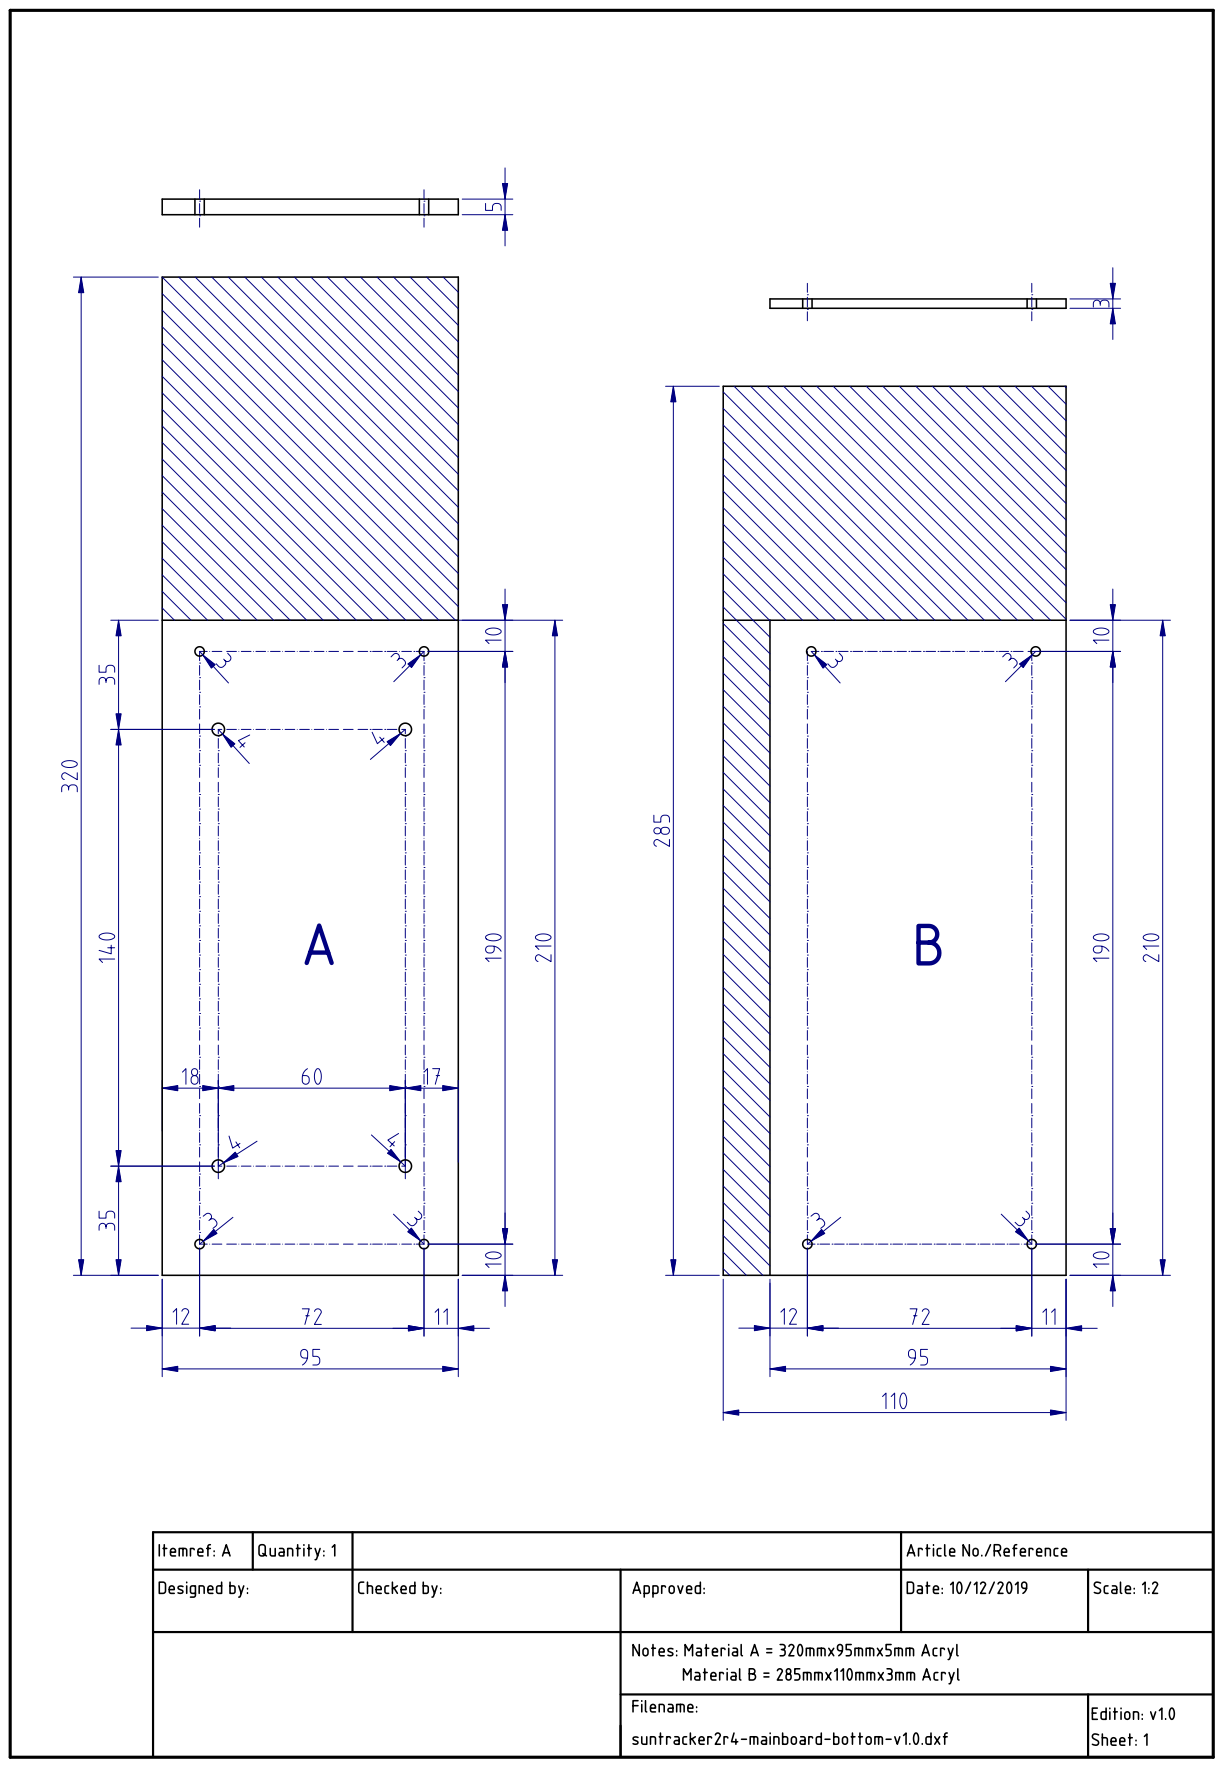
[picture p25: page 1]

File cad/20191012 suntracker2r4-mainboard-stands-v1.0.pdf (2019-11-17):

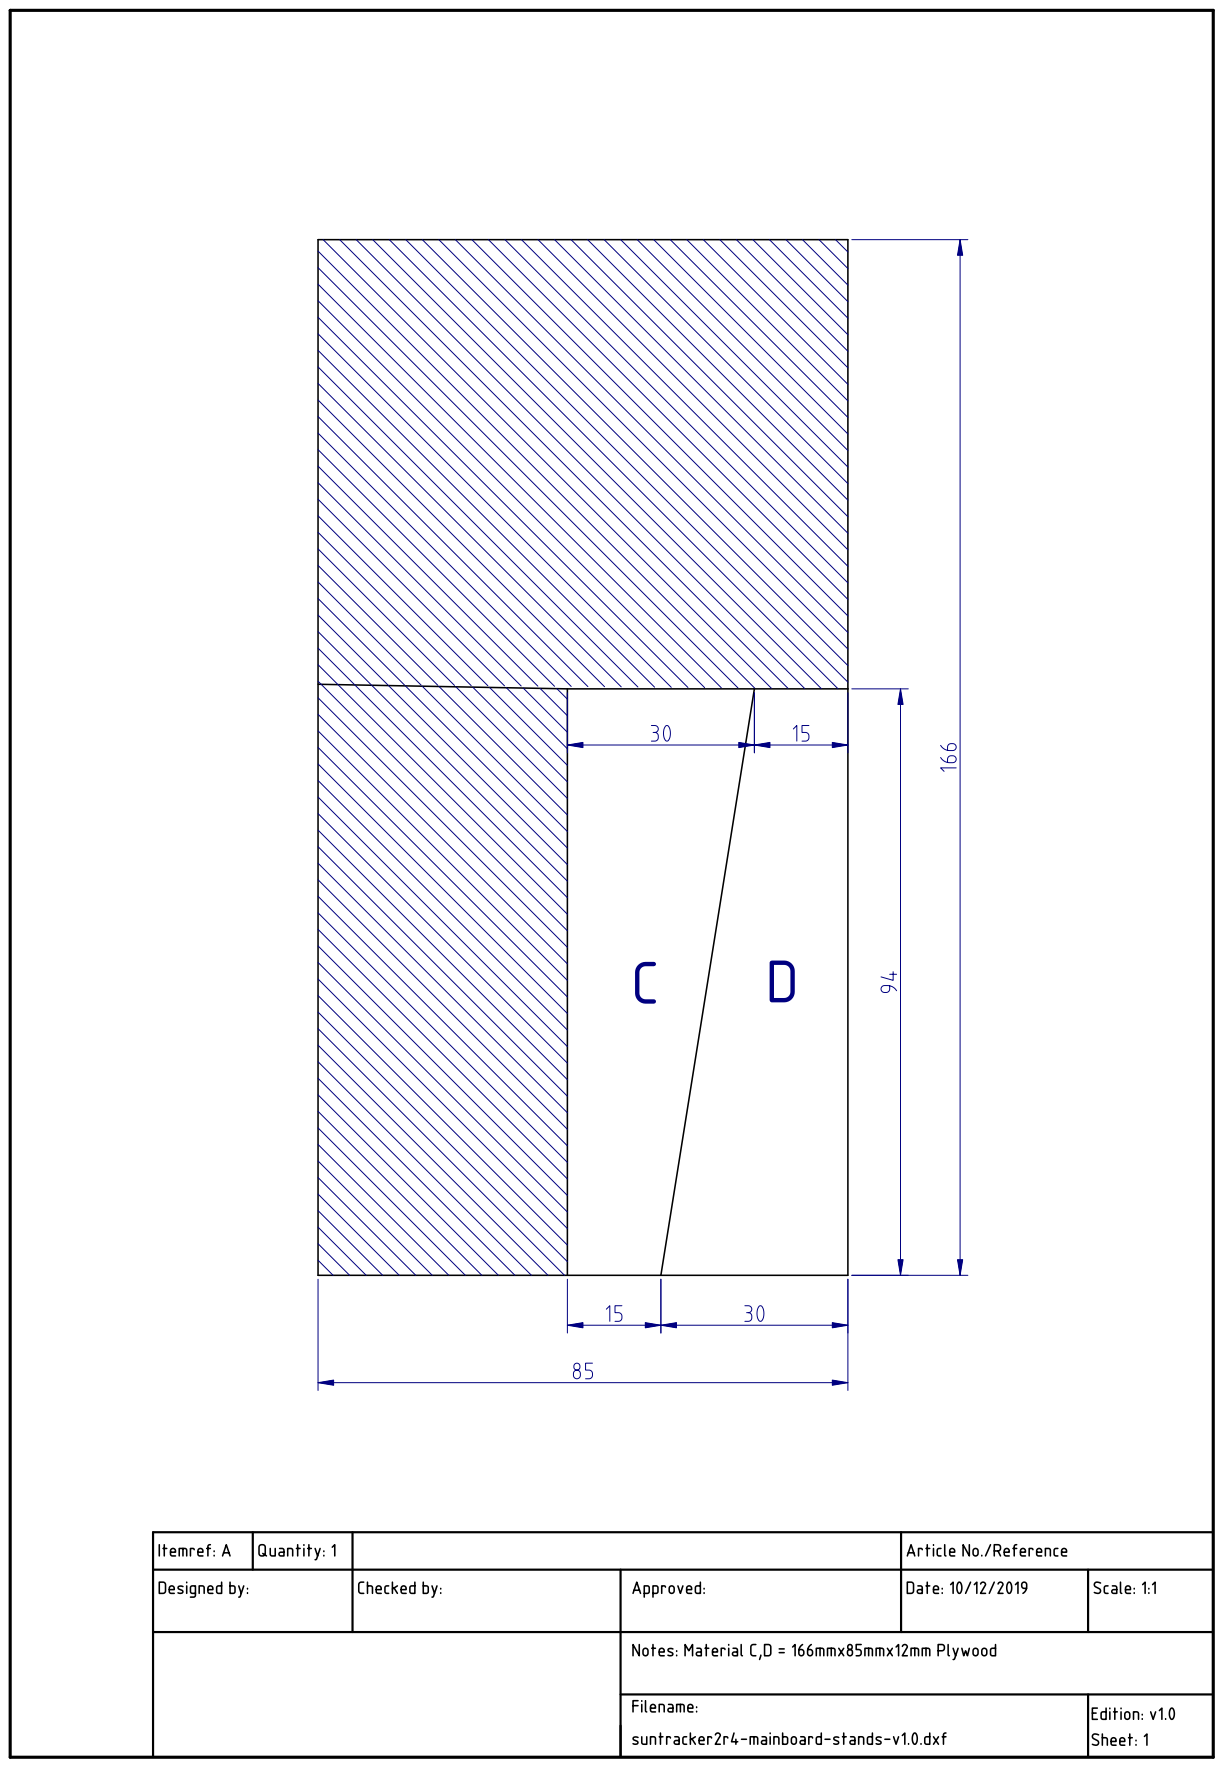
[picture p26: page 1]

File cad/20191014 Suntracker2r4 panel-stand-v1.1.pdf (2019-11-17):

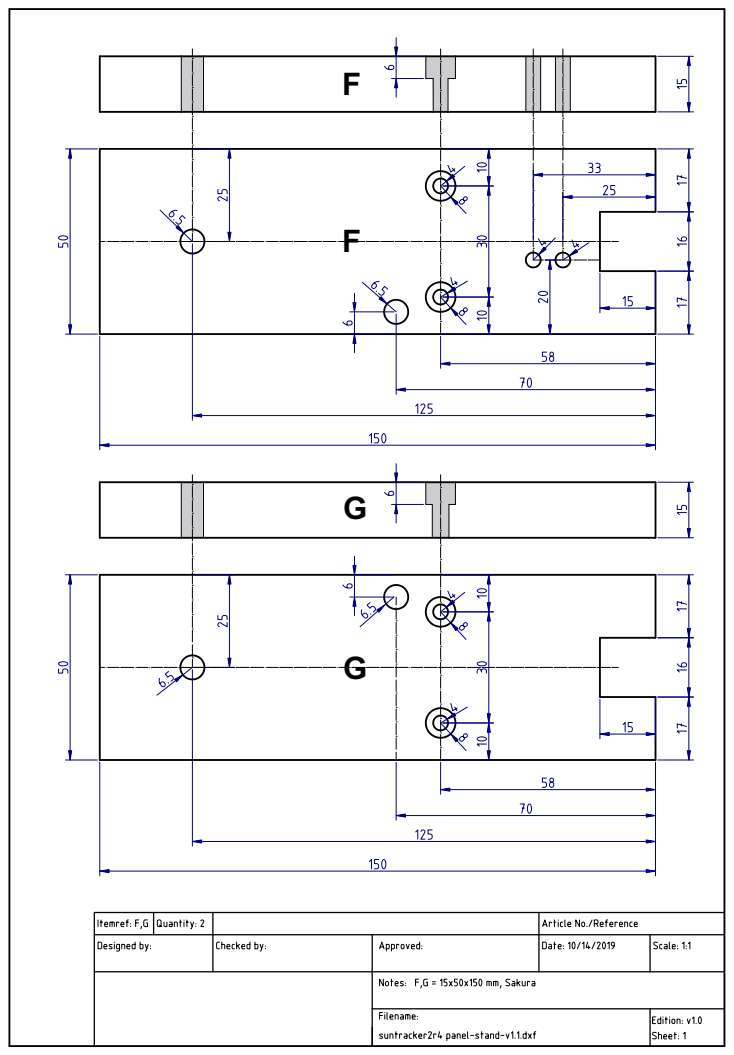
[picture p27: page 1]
FGFG

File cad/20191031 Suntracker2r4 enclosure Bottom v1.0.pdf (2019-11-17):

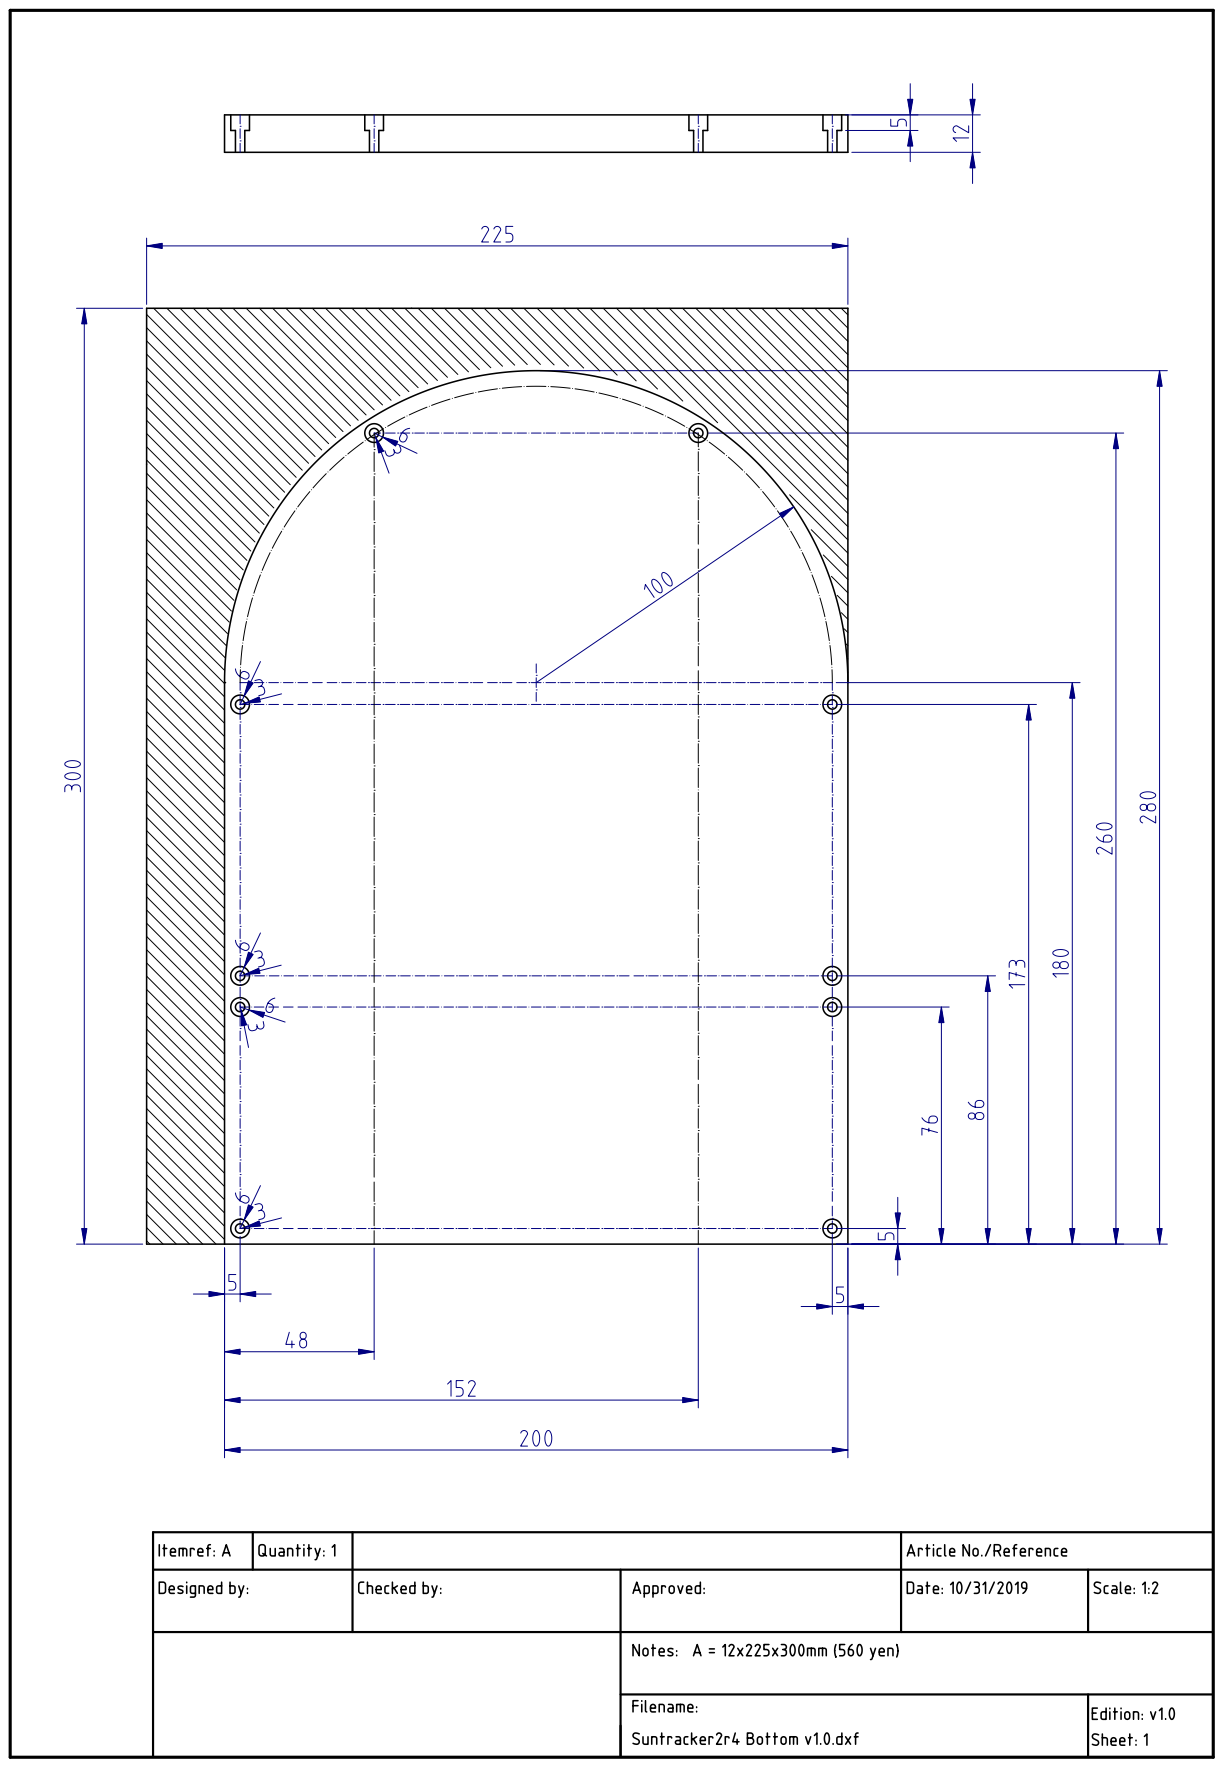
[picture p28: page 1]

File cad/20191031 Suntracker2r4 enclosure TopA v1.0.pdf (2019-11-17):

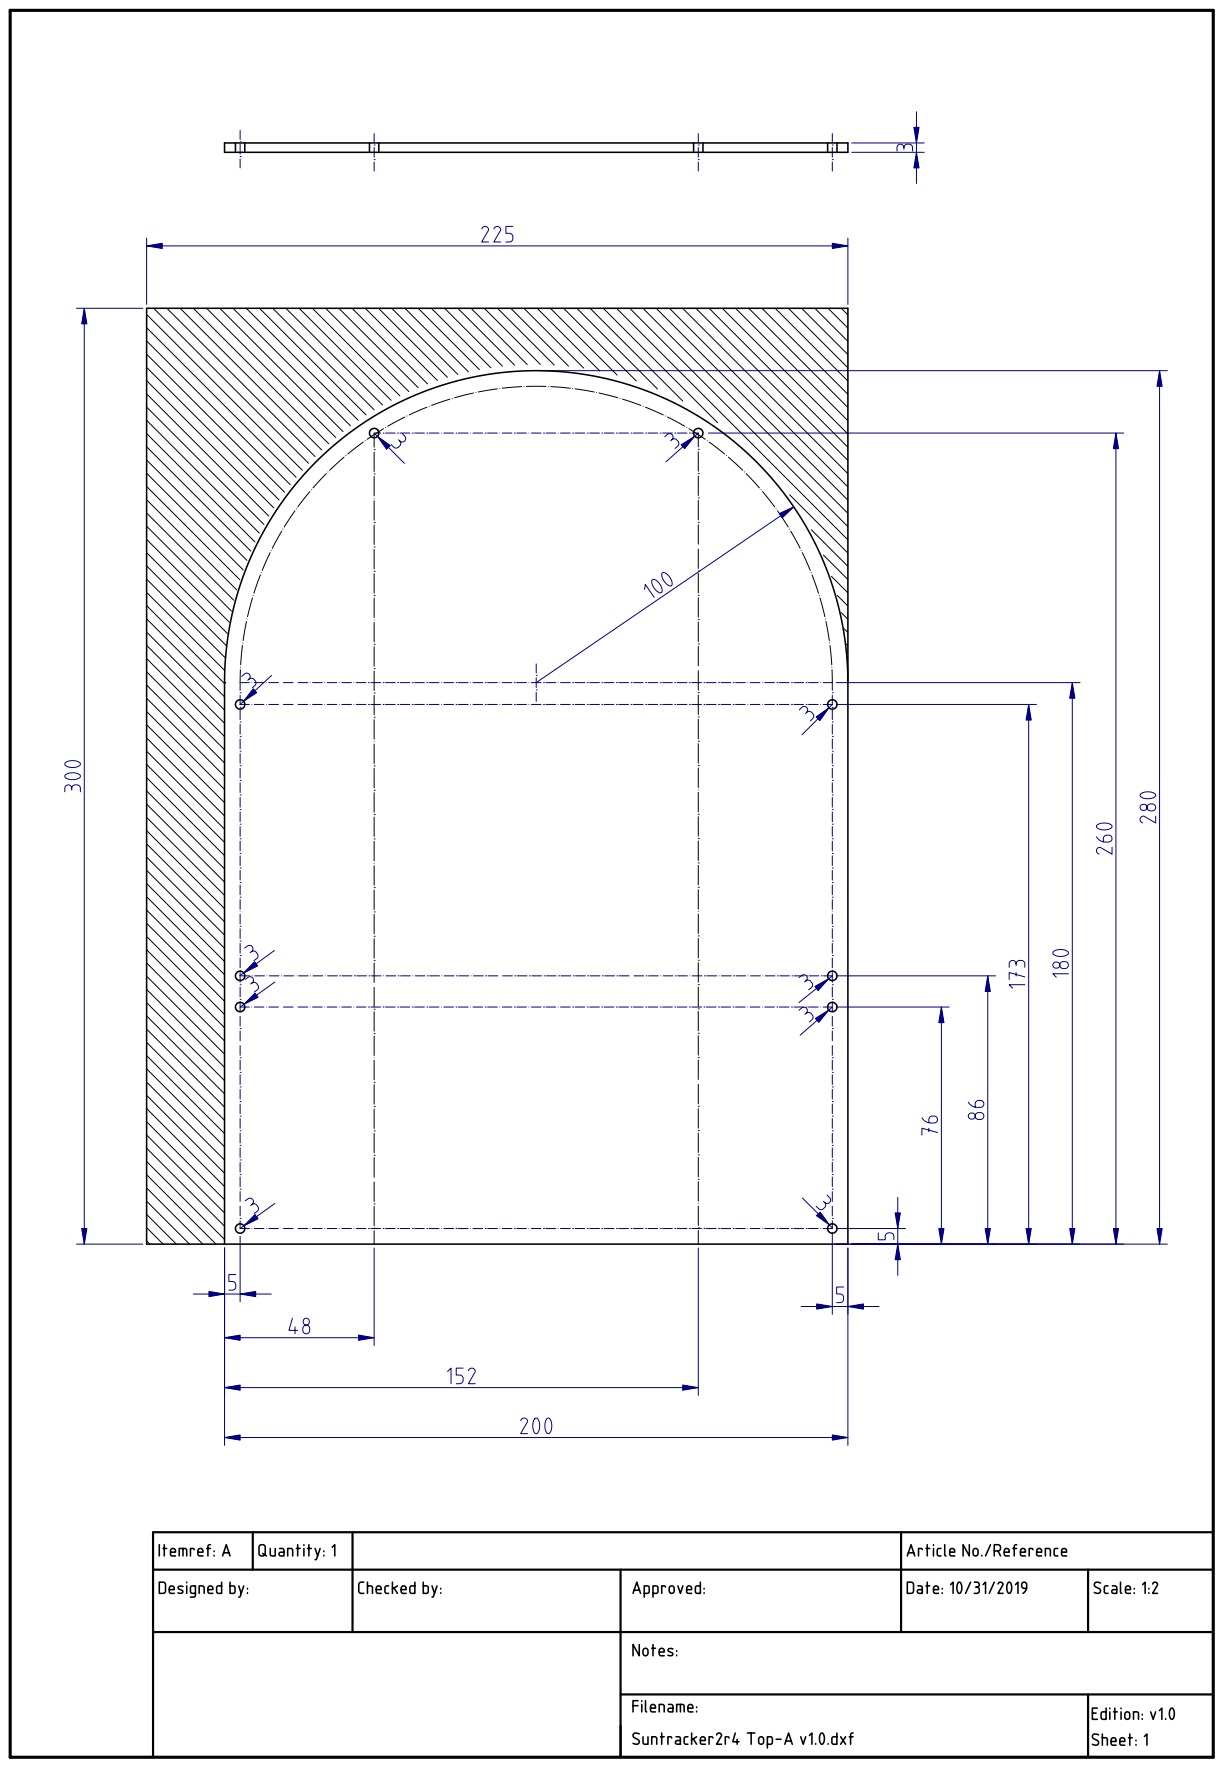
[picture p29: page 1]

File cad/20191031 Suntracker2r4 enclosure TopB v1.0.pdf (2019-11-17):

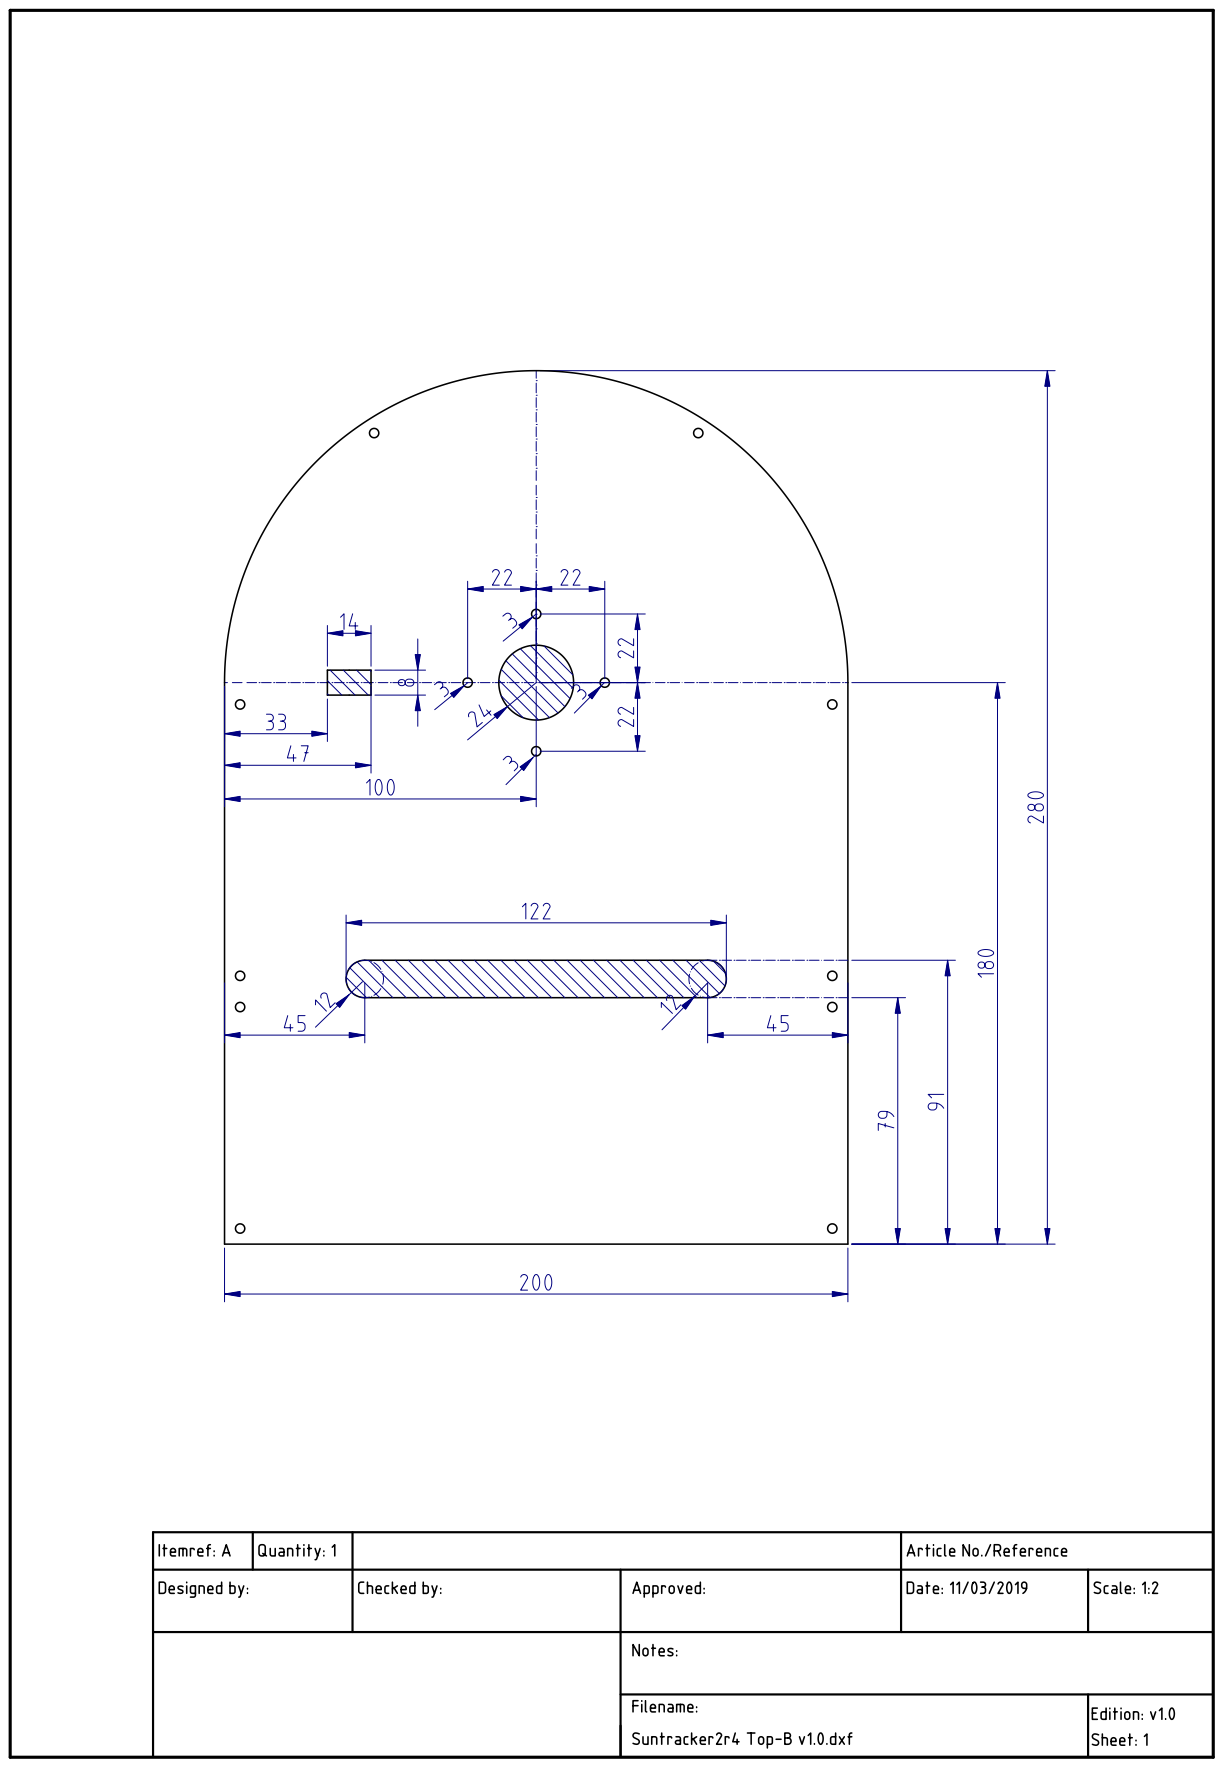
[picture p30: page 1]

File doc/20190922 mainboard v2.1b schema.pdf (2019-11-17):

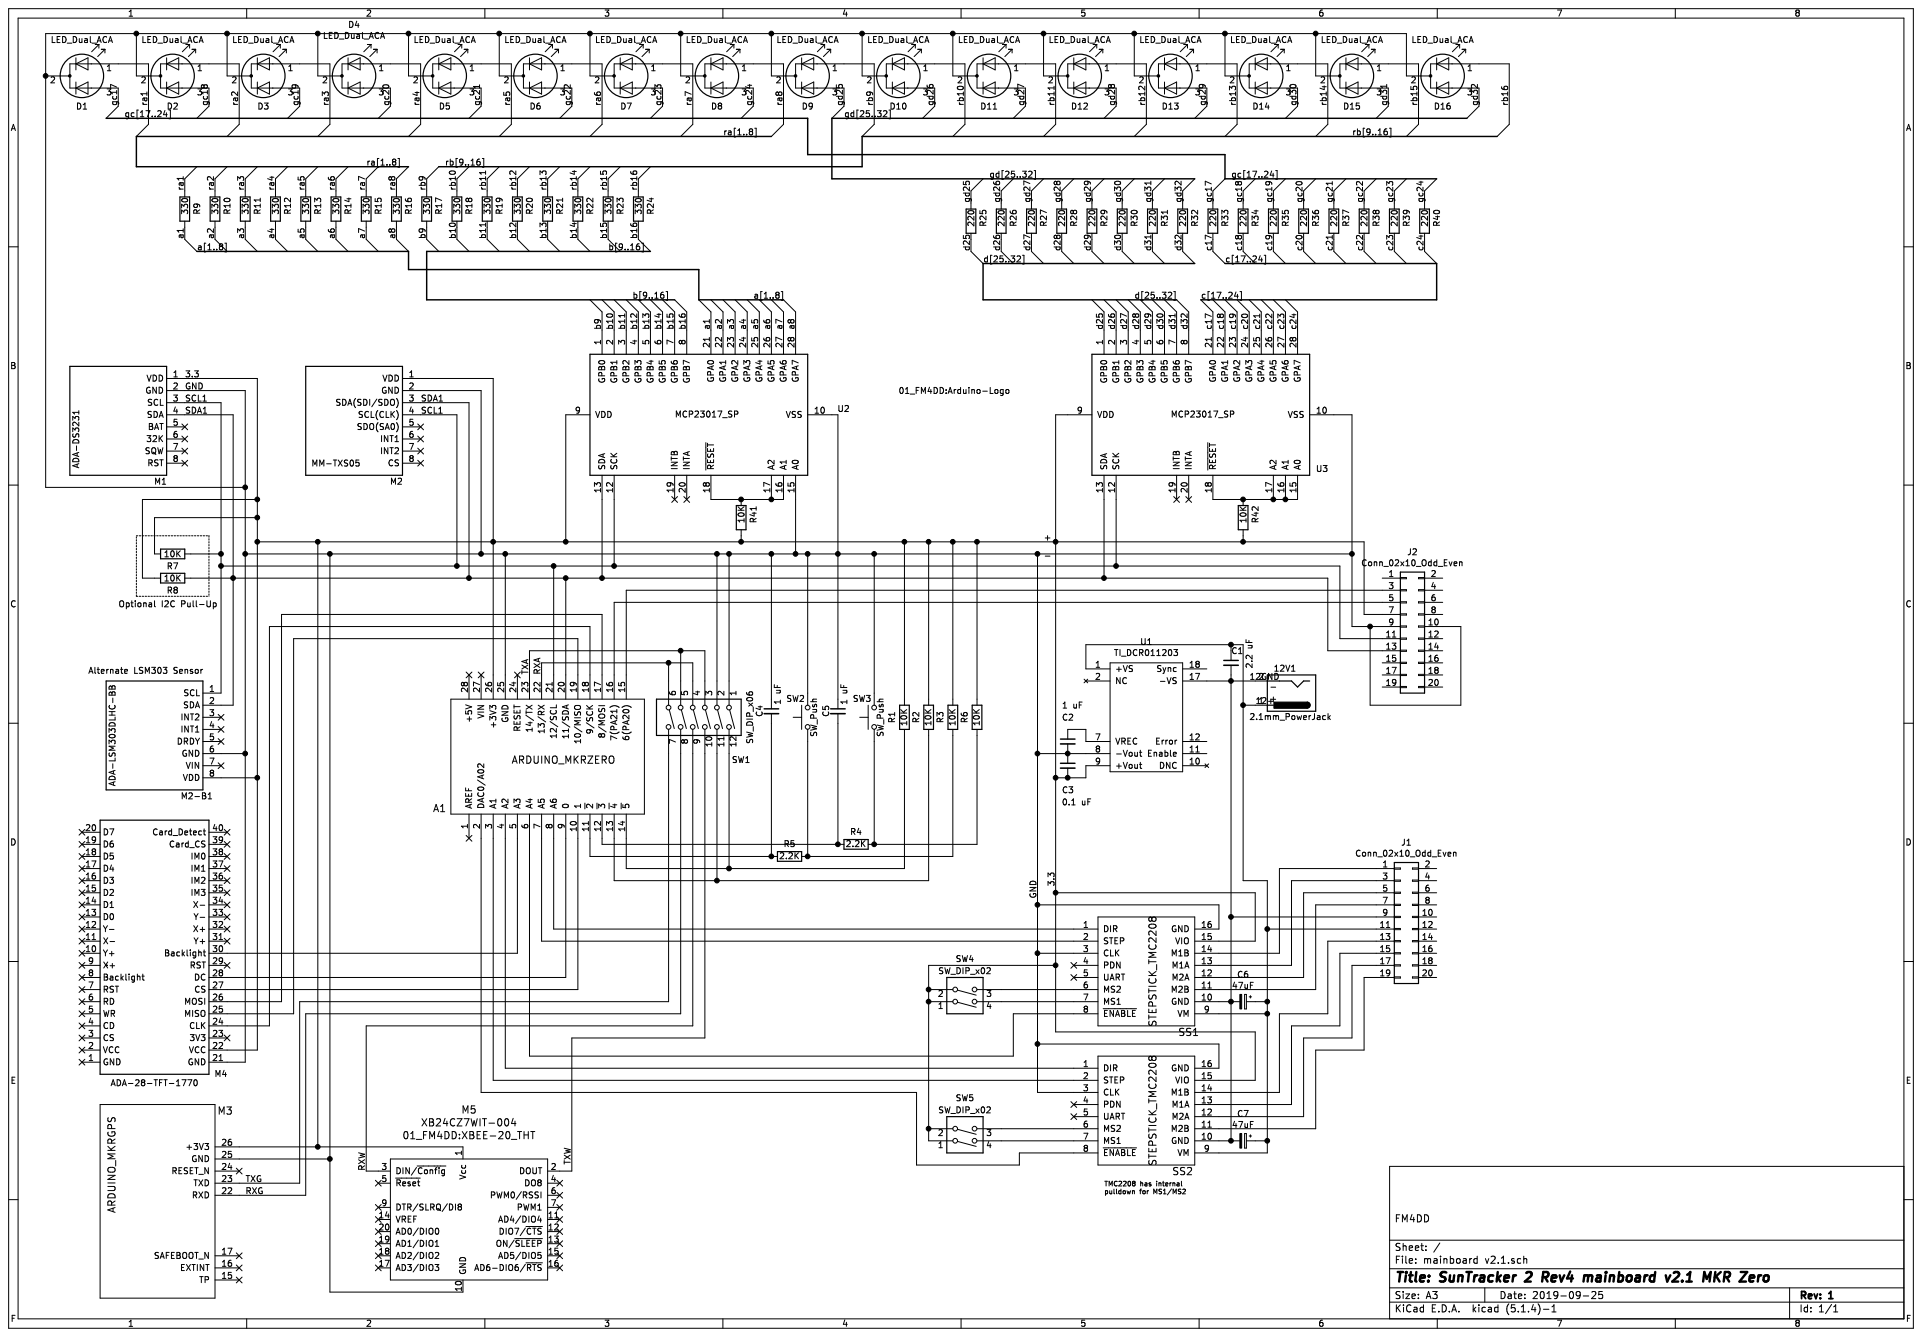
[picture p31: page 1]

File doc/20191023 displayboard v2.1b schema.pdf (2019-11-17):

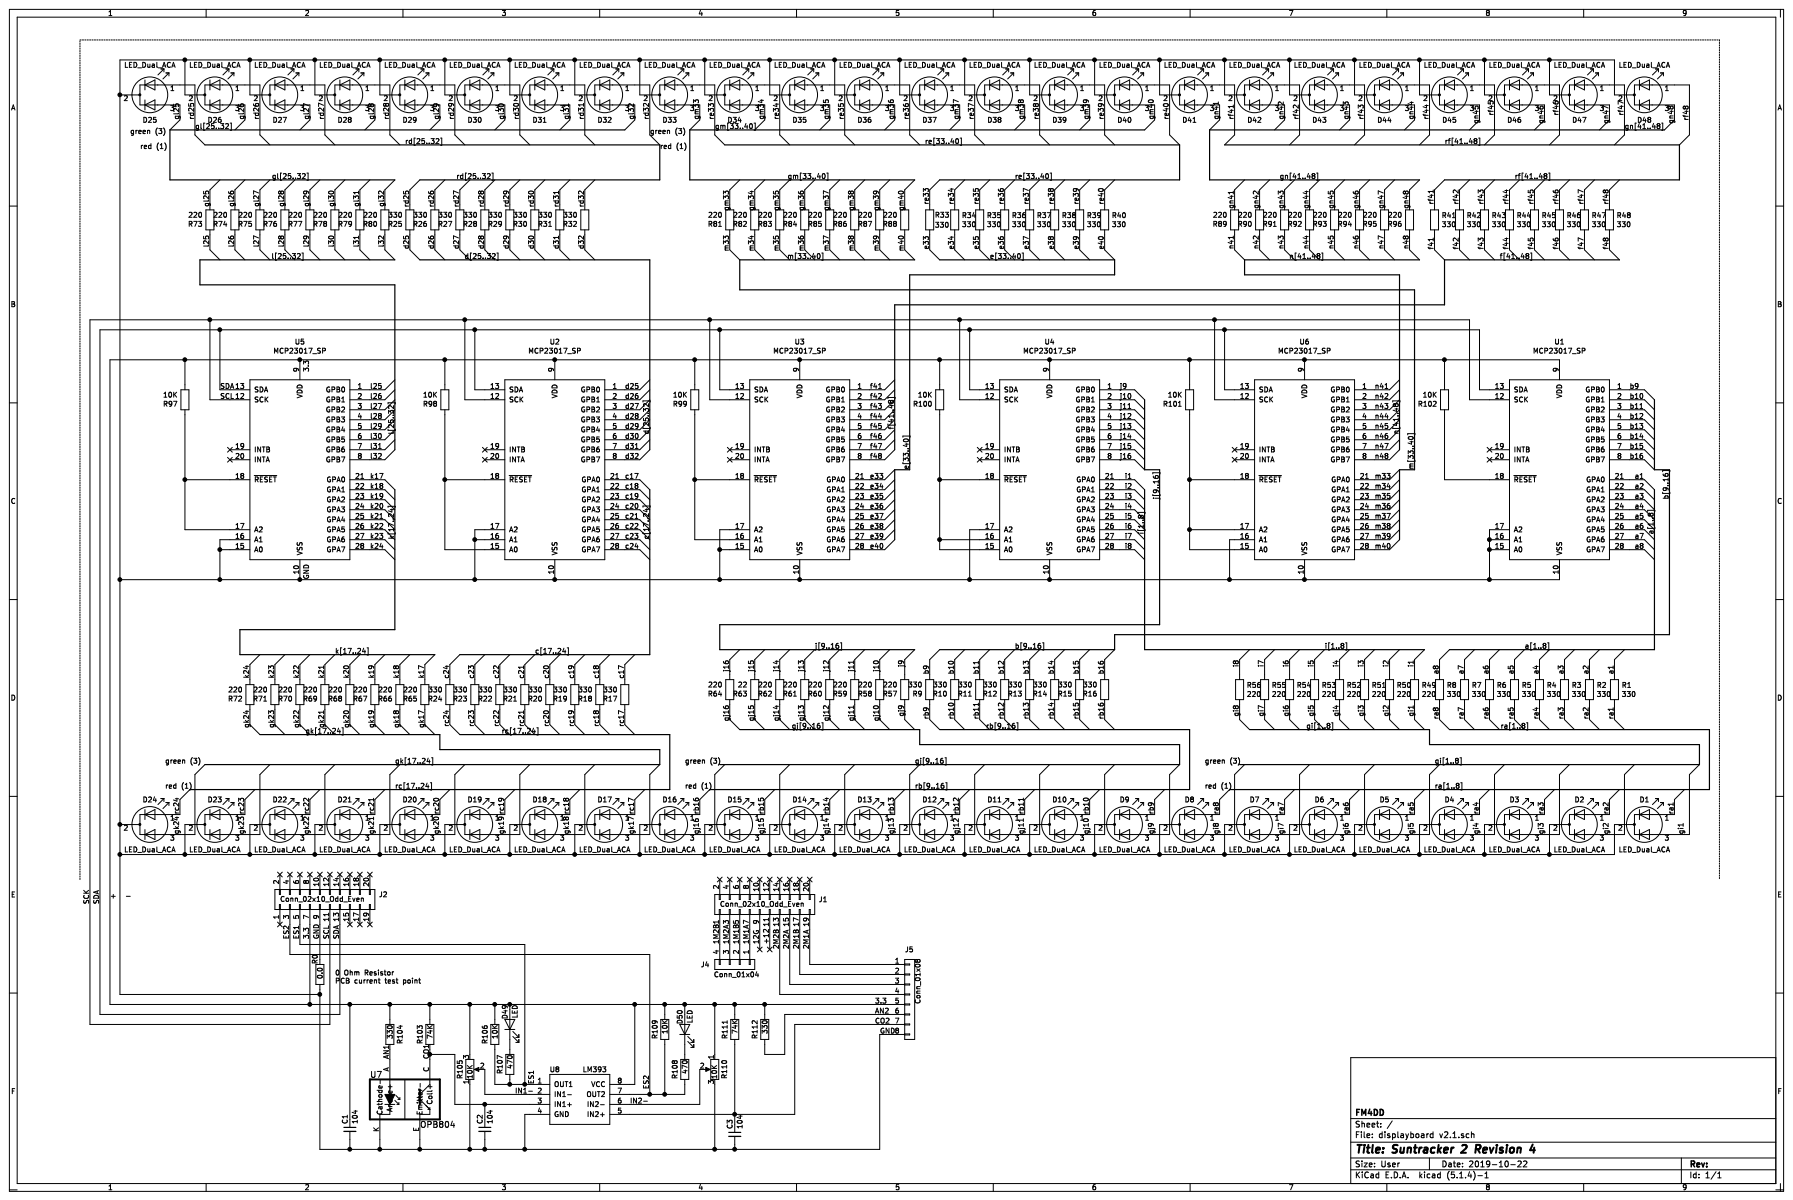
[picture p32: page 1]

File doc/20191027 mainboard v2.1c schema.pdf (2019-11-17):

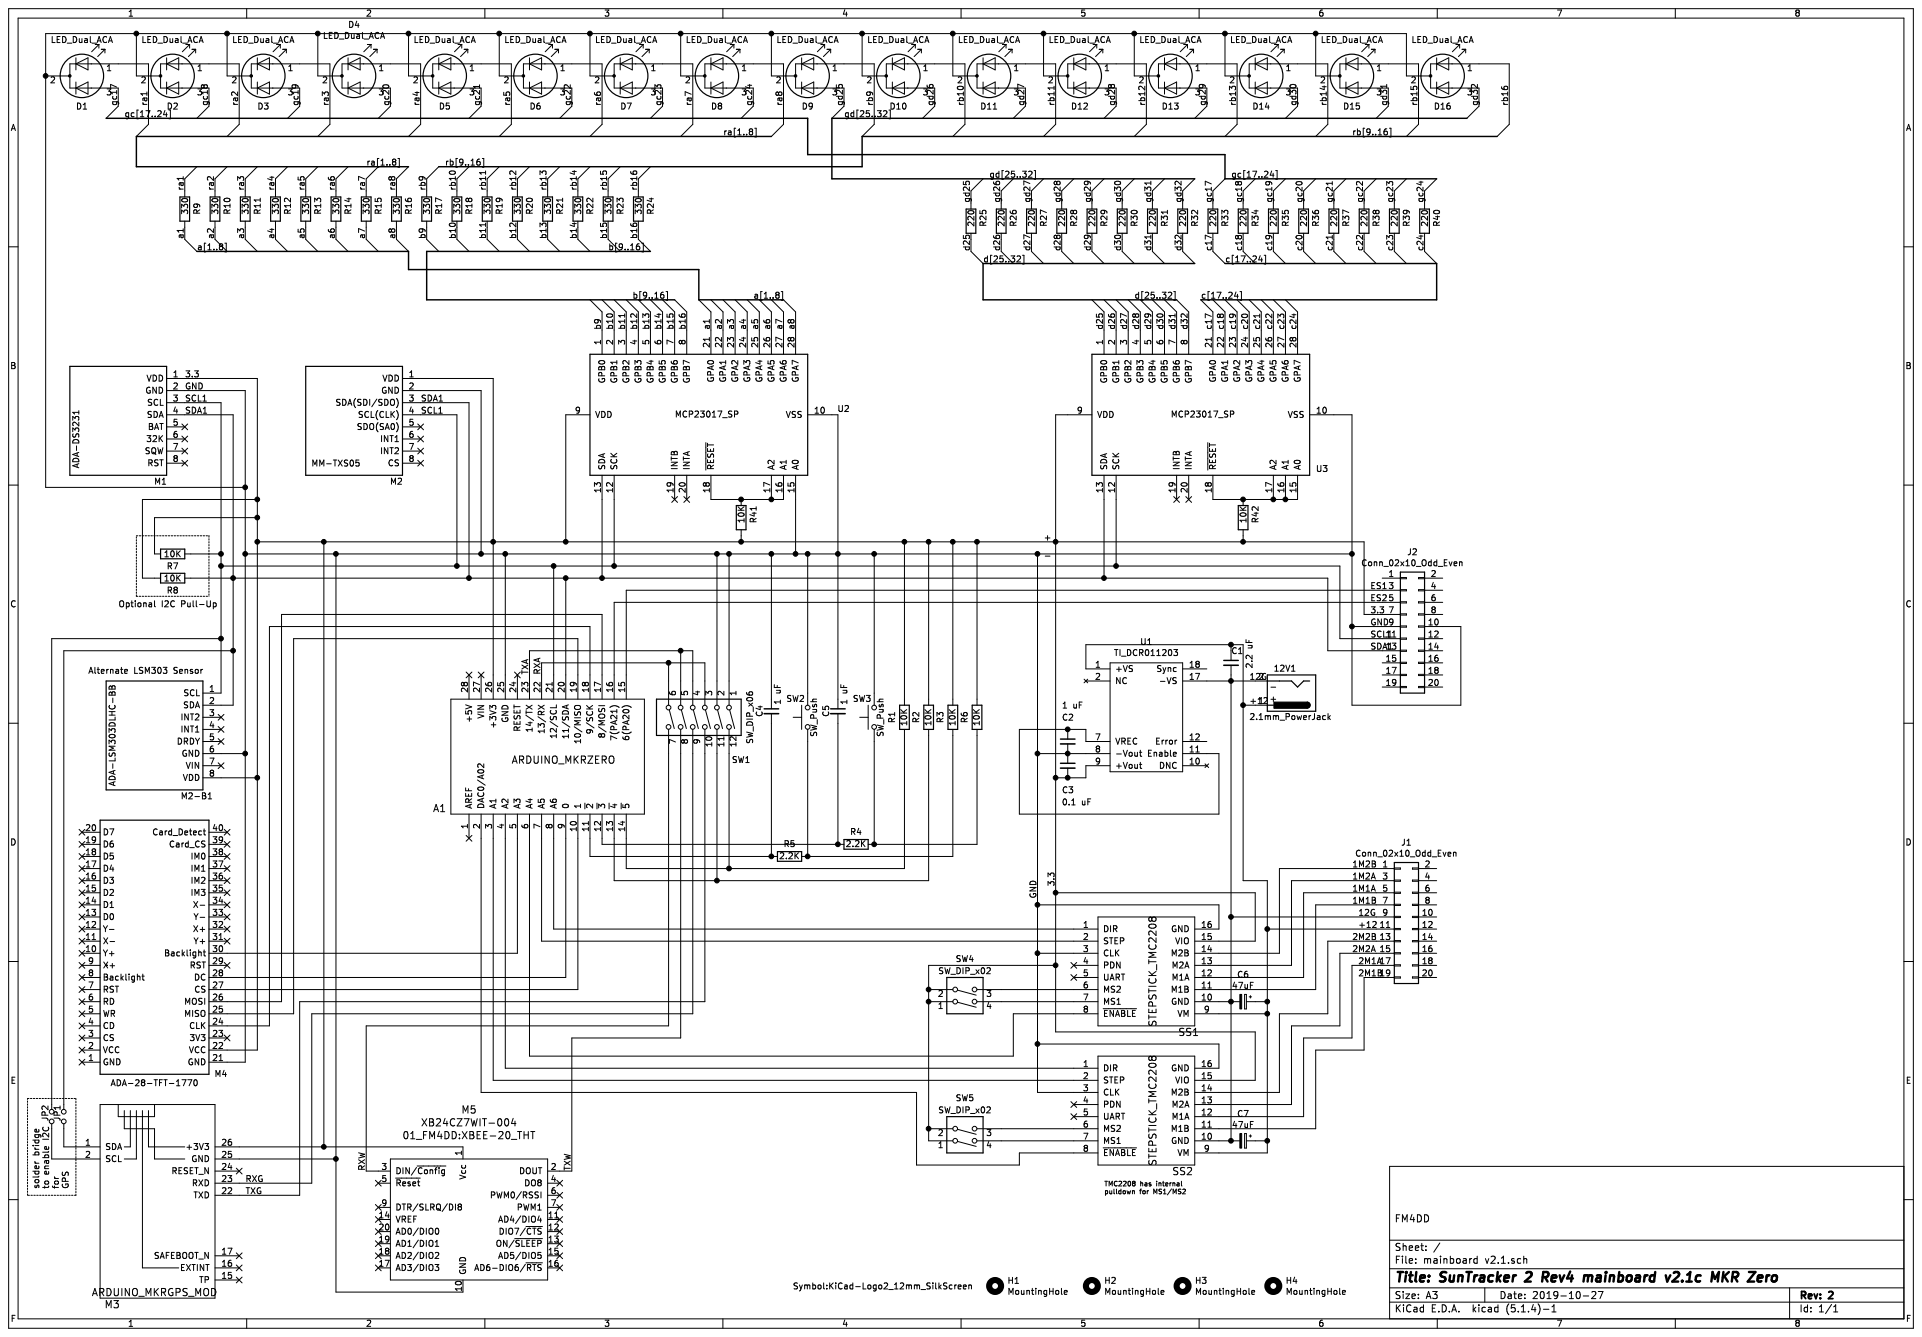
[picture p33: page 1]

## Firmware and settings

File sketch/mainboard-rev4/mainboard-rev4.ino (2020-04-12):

/* ------------------------------------------------- *
 * Suntracker2  mainboard-rev4  Oct 2019 @ FM4DD     *
 *                                                   * 
 * This code controls Suntracker2 mainboard v2.1 and *
 * displayboard v2.1 for dual angle zenith + azimuth *
 * tracking. Requires suncalc v1.2 generated solar   *
 * position data stored on the MKRZERO MicroSD card. *
 * ------------------------------------------------- */
#include "Arduino_MKRGPS.h" // Arduino GPS library
#include <avr/dtostrf.h>    // dtostrf float conversion
#include "globals.h"        // global variable definitions
#include "demo.h"           // demo mode function

// write board settings and serial to sdcard file
struct s2r4_settings {
  byte serial;
  byte field2;
  char name[10];
};

/* ------------------------------------------------- */
/* Object class instances                            */
/* ------------------------------------------------- */
ledRow row;               // 16-LED eleveation row
ledRing ring;             // 48-LED azimuth ring
AMotor amotor;            // azimuth motor
ZMotor zmotor;            // azimuth motor
Demo demo;                // demo mode
Display display;          // TFT display
Sd2Card card;             // SD card
SdVolume volume;          // SD partition
SdFile root;              // SD filesystem
LSM303 compass;           // Magnetic field Sensor
uRTCLib rtc;              // DS3231 Precision RTC clock
XBee xbee;                // XBee S2C wireless comms
/* ------------------------------------------------- */
/* DEBUG enables debug output to the serial monitor  */
/* ------------------------------------------------- */
//#define DEBUG

void setup() {
#ifdef DEBUG
  /* ------------------------------------------------- */
  /* Enable Serial Debug output                        */
  /* ------------------------------------------------- */
  Serial.begin(9600);
  while (!Serial);   // wait for serial port to connect.
  Serial.println("Serial Debug Start");
#endif
  /* ------------------------------------------------- */
  /* Enable TFT display, clear screen, set black bgnd  */
  /* ------------------------------------------------- */
  digitalWrite(TFT_BL, LOW);  // Set LOW before OUTPUT
  pinMode(TFT_BL, OUTPUT);    // to prevent screen on
  display.enable();
  digitalWrite(TFT_BL, HIGH);
  display.bmpDraw("S2R4IMG.BMP", 0, 0);
  display.show_ver();
  delay(8000);
  display.header();
  display.opmode(opmode);
  delay(1000);
  /* ------------------------------------------------- */
  /* Set dipswitch GPIO ports as input                 */
  /* ------------------------------------------------- */
  pinMode(DIP1, INPUT);
  pinMode(DIP2, INPUT);
  dippos1 = digitalRead(DIP1);
  dippos2 = digitalRead(DIP2);    
  /* ------------------------------------------------- */
  /* Set pushbutton GPIO ports as input                */
  /* ------------------------------------------------- */
  pinMode(PUSH1, INPUT);
  pinMode(PUSH2, INPUT);
  /* ------------------------------------------------- */
  /* Pushbutton 1 (-) at startup triggers demo LOW=ON  */
  /* demo mode switches main loop from min to sec exec */
  /* ------------------------------------------------- */
  if(digitalRead(PUSH1) == LOW) opmode = 2; // demo mode
  /* ------------------------------------------------- */
  /* Pushbutton 2 (-) at startup for extended selftest */
  /* LOW=ON. Ext. Selftest runs extra checks at bootup */
  /* ------------------------------------------------- */
  if(digitalRead(PUSH2) == LOW) testmode = 1; // extended
  /* ------------------------------------------------- */
  /* Enable I2C bus                                    */
  /* ------------------------------------------------- */
  Wire.begin();
  /* ------------------------------------------------- */
  /* Pushbutton 2 at boot sets testmode. 1 = extended  */
  /* ------------------------------------------------- */
  if(testmode == 1) {
    u8g2_tft.drawStr(0, 100, "Modules Test:");
    /* ------------------------------------------------- */
    /* Identify I2C devices                              */
    /* 0x19 = LSM303DLHC Accel (Adafruit product: 1120)  */
    /* 0x1D = LSM303D (Sunhayato MM-TXS05 module)        */
    /* 0x1E = LSM303DLHC Mag (Adafruit product: 1120)    */
    /* 0x20 .. 0x27 = MCP23017 1-8                       */
    /* 0x42 = Arduio MKR GPS Shield on I2C               */
    /* 0x68 = DS3231 RTC                                 */
    /* ------------------------------------------------- */
    const int size = 12; // # of I2C devices to check for
    byte addr[size] = { 0x1D, 0x1E, 0x20, 0x21, 0x22, 0x23, 
                        0x24, 0x25, 0x26, 0x27, 0x42, 0x68 };
    int i;
    int line = 100;
    byte error;
    for(i = 0; i<size; i++ ) {
      /* ------------------------------------------------- */
      /* The i2c_scanner uses the Write.endTransmisstion   */
      /* return value to see if device exists at the addr  */
      /* ------------------------------------------------- */
      snprintf(lineStr, sizeof(lineStr), "I2C check %02x: ", addr[i]);
      line = line + 20;
      if (line > 239) {
        display.wipe();
        line = 100; 
      }
      u8g2_tft.drawStr(0, line, lineStr);
      Wire.beginTransmission(addr[i]);
      error = Wire.endTransmission();

      if (error == 0){
        snprintf(lineStr, sizeof(lineStr), "%02x Response OK", addr[i]);
        u8g2_tft.drawStr(150, line, lineStr);
      }
      else if (error==4) {
        snprintf(lineStr, sizeof(lineStr), "%02x Error      ", addr[i]);
        u8g2_tft.drawStr(150, line, lineStr);
      }
      else {
        snprintf(lineStr, sizeof(lineStr), "%02x Not Found  ", addr[i]);
        u8g2_tft.drawStr(150, line, lineStr);
      }
      delay(1000);
    }
    delay(2000);
    display.wipe();
  } // end testmode = 1, skip extended selftest
  /* ------------------------------------------------- */
  /* Enable the SD card module                         */
  /* ------------------------------------------------- */
  u8g2_tft.drawStr(0, 93, "Init SD card:");
  if (!card.init(SPI_HALF_SPEED, SDCARD_SS_PIN)) {
    u8g2_tft.drawStr(150, 93, "SD card FAIL  ");
    while(1);
  } else {
    switch (card.type()) {
      case SD_CARD_TYPE_SD1:
        Serial.println("SD1");
        u8g2_tft.drawStr(150, 93, "SD1 card OK   ");
        break;
      case SD_CARD_TYPE_SD2:
        u8g2_tft.drawStr(150, 93, "SD2 card OK   ");
        break;
      case SD_CARD_TYPE_SDHC:
        u8g2_tft.drawStr(150, 93, "SDHC card OK  ");
        break;
      default:
        u8g2_tft.drawStr(150, 93, "Unknown card  ");
    }
  }
  SD.begin(SDCARD_SS_PIN); 
  delay(500);
  u8g2_tft.drawStr(150, 93, "Read file dset.txt.");
  File dset = SD.open("DSET.TXT");
  int i = 0;
  if(dset) {
    unsigned long fsize = dset.size();
    snprintf(lineStr, sizeof(lineStr), "DSET.TXT %ld bytes OK", fsize);
    u8g2_tft.drawStr(150, 93, lineStr);
    delay(2000);
//while (dset.available()) {
//        dset.readStringUntil(':').toCharArray(lineStr,15);
//        u8g2_tft.drawStr(0, 100+(i*20), lineStr);
//        dset.read(lineStr, 1); // skip over one space
//        dset.readStringUntil('\n').toCharArray(lineStr,15);
//        u8g2_tft.drawStr(150, 100+(i*20), lineStr);
//        delay(1000);
//        i++;
//      }
    } else {
      u8g2_tft.drawStr(150, 93, "Fail open dset.txt");
    }
    dset.close();
  /* ------------------------------------------------- */
  /* Enable the DS3231 RTC clock module                */
  /* ------------------------------------------------- */
  u8g2_tft.drawStr(0, 111, "Init DS3231:");
  Wire.beginTransmission(0x68);
  if (Wire.endTransmission() == 0) {
    rtc.set_rtc_address(0x68);
    rtc.set_model(URTCLIB_MODEL_DS3231);
    /* ------------------------------------------------- */
    /* To set the initial time, enable the line below    */
    /* set(sec,min,hour,dayOfWeek,dayOfMonth,month,year) */
    /* ------------------------------------------------- */
    //rtc.set(0, 3, 18, 1, 4, 11, 19);
    rtc.refresh();
    snprintf(lineStr, sizeof(lineStr), "20%02d/%02d/%02d %02d:%02d",
    rtc.year(),rtc.month(),rtc.day(),rtc.hour(),rtc.minute());
  }
  else {
    snprintf(lineStr, sizeof(lineStr), "No RTC I2C 0x68");
  }
  u8g2_tft.drawStr(150, 111, lineStr);
  delay(1500);
  /* ------------------------------------------------- */
  /* Enable the LSM303 Compass sensor module           */
  /* 1. Sunhayato MM-TXS05 SA0 default I2C addr (0x1D) */
  /* compass.init(LSM303::device_D,LSM303::sa0_high);  */
  /* 2. Adafruit LSM303DLHC module (PROD-ID 1120) use: */
  /* compass.init(LSM303::device_DLHC,LSM303::sa0_high);*/
  /* init() without args tries to determine chip type  */
  /* ------------------------------------------------- */
  boolean mag_found = false;
  u8g2_tft.drawStr(0, 129, "Init Compass:");
  mag_found = compass.init();
  if(mag_found) {
    if(compass.getDeviceType() == 3) u8g2_tft.drawStr(150, 129, "SH MM-TXS05");
    else 
      if(compass.getDeviceType() == 2) u8g2_tft.drawStr(150, 129, "ADA-LSM303");
    compass.enableDefault();
    /* ------------------------------------------------- */
    /* LSM303D Calibration values, see Calibrate example */
    /* ------------------------------------------------- */
    //compass.m_min = (LSM303::vector<int16_t>){-2246, -1776, -4034};
    //compass.m_max = (LSM303::vector<int16_t>){+2463, +2870,  +822};
    // Board 2 - Adafruit SLM303DLHC
    compass.m_min = (LSM303::vector<int16_t>){-595, -511, -445};
    compass.m_max = (LSM303::vector<int16_t>){+589, +597, +573};
    u8g2_tft.drawStr(257, 129, "Init OK");
    /* ------------------------------------------------- */
    /* Aquire compass sensor data                        */
    /* ------------------------------------------------- */
    compass.read();
    if(compass.getDeviceType() == 3) heading = compass.heading() + mdecl;
    if(compass.getDeviceType() == 2) heading = compass.heading((LSM303::vector<int>){1,0,0}) + mdecl;
    if(heading < 0) heading = 360.0 + heading;
    /* ------------------------------------------------- */
    /* print North heading to TFT                        */
    /* ------------------------------------------------- */
    dtostrf(heading,6,4,lineStr);
    u8g2_tft.drawStr(257,129, lineStr);
  }
  else {
    u8g2_tft.drawStr(150, 129, "LSM303 Not Found!");
  }
  delay(1500);
  /* ------------------------------------------------- */
  /* Enable MKRGPS with I2C DDC protocol               */
  /* ------------------------------------------------- */
  u8g2_tft.drawStr(0, 147, "Init GPS I2C:");
  Wire.beginTransmission(0x42);
  if (Wire.endTransmission() == 0) {
    GPS.begin(GPS_MODE_I2C);
    /* ------------------------------------------------- */
    /* Aquire GPS sensor data                            */
    /* ------------------------------------------------- */
    if (GPS.available()) {
      latitude   = GPS.latitude();
      longitude  = GPS.longitude();
      altitude   = GPS.altitude();
      speed      = GPS.speed();
      satellites = GPS.satellites();
    }
    char latStr[16];
    String(latitude, 8).toCharArray(latStr, 8);
    char lonStr[16];
    String(longitude, 8).toCharArray(lonStr, 8);
    snprintf(lineStr, sizeof(lineStr), "%d Satellites", satellites);
    u8g2_tft.drawStr(150, 147, lineStr);
    snprintf(lineStr, sizeof(lineStr), "LAT: %s", latStr);
    u8g2_tft.drawStr(0, 165, lineStr);
    snprintf(lineStr, sizeof(lineStr), "LON: %s", lonStr);
    u8g2_tft.drawStr(150, 165, lineStr);
  }
  else {
    u8g2_tft.drawStr(150, 147, "No GPS Shield 0x42");
  }
  delay(500);
  /* ------------------------------------------------- */
  /* Test XBee S2C wireless commuication module        */
  /* ------------------------------------------------- */
  u8g2_tft.drawStr(0, 183, "Init XBee S2C:");
  if(xbee.enable() == true) {
    u8g2_tft.drawStr(150, 183, "Module OK ");
    if(xbee.getstatus() == true) {
      if(xbee.getassociation() == 0)
        snprintf(lineStr, sizeof(lineStr),
          "Network %d ONLINE", xbee.getoper_panid());
      u8g2_tft.drawStr(150, 183, lineStr);
    }
  }
  else
    u8g2_tft.drawStr(150, 183, "Module N/A");
  /* ------------------------------------------------- */
  /* Test mainboard zenith row IO expanders            */
  /* ------------------------------------------------- */
  u8g2_tft.drawStr(0, 201, "Init LED Row:");
  if(row.enable() == 0) {
    u8g2_tft.drawStr(150, 201, "I2C 0x26/27 OK ");
    /* ----------------------------------------------- */
    /* Test LED row                                    */
    /* ----------------------------------------------- */
    u8g2_tft.drawStr(0, 219, "Test LED Row: ");
    delay(500);
    u8g2_tft.drawStr(150, 219, "Zenith Row RED  ");
    row.stepled_red(50);
    u8g2_tft.drawStr(150, 219, "Zenith Row GREEN");
    row.stepled_green(50);
    u8g2_tft.drawStr(150, 219, "Zenith Row ALL  ");
    row.lightcheck();
    u8g2_tft.drawStr(150, 219, "Zenit Row done  ");
  }
  else
    u8g2_tft.drawStr(150, 201, "I2C 0x26/27 ERR");
  delay(500);
  
  /* ------------------------------------------------- */
  /* Test if displayboard is connected                 */
  /* ------------------------------------------------- */
  u8g2_tft.drawStr(0, 237, "Init LED Ring:");
  if(ring.enable() == 0) {
    u8g2_tft.drawStr(150, 237, "I2C 0x20-25 OK ");
    /* ----------------------------------------------- */
    /* Test LED ring                                   */
    /* ----------------------------------------------- */
    u8g2_tft.drawStr(0, 237, "Test LED Ring:");
    u8g2_tft.drawStr(150, 237, "                ");
    u8g2_tft.drawStr(150, 237, "Lightshow ON"); 
    ring.lightshow(40);
  }
  else
    u8g2_tft.drawStr(150, 237, "I2C 0x20-25 ERR");
  delay(3500);
  display.wipe();
  /* ------------------------------------------------- */
  /* 2nd dip switch enables the motor function, LOW=ON */
  /* ------------------------------------------------- */
  if(dippos2 == LOW) {
    amotor.enable();
    zmotor.enable();
    /* ----------------------------------------------- */
    /* Motor1 testing                                  */
    /* ----------------------------------------------- */
    u8g2_tft.drawStr(0, 100, "Test Stepper-1:");
    amotor.sethome(SLOW); /* bring motor home if reqrd */
    delay(500);
    zmotor.demoturn(2);   /* test motor for 2x times   */
    u8g2_tft.drawStr(150, 100, "Complete");
    delay(1000);
    m1cpos = 0;    /* Set motor1 current position = D1 */
    m1tpos = 0;    /* Set motor1 target position = D1  */
    m2cpos = 0;    /* Set motor1 current position = D1 */
    m2tpos = 0;    /* Set motor1 target position = D1  */
  }
  /* ------------------------------------------------- */
  /* Read sunrise sunset time from SRS-<YYYY>.BIN file */
  /* ------------------------------------------------- */
  snprintf(srsfile, sizeof(srsfile), "SRS-20%02d.BIN", rtc.year());
  get_suntime(srsfile);
  /* ------------------------------------------------- */
  /* Set daily data file name per RTC current date     */
  /* ------------------------------------------------- */
  snprintf(binfile, sizeof(binfile), "20%02d%02d%02d.BIN", 
             rtc.year(),rtc.month(),rtc.day());
  /* ------------------------------------------------- */
  /* Check for demo mode                               */
  /* ------------------------------------------------- */
  if(opmode == 2) {
    /* ----------------------------------------------- */
    /* If demo mode was requested, set TFT mode state  */
    /* ----------------------------------------------- */
    display.wipe();
    display.opmode(opmode);
    demo.run();
  }
  delay(3000);
  /* ------------------------------------------------- */
  /* Intitialize azimuth/elevation position from file  */
  /* ------------------------------------------------- */
  rtc.refresh();
  solar_position(binfile);
  /* ------------------------------------------------- */
  /* Clear TFT section below header                    */
  /* ------------------------------------------------- */
  display.wipe();
  opmode = 1;
  display.opmode(opmode);
  display.show_date();     // show date
  display.show_rise_set(); // show sunrise/sunset
  display.show_transit();  // show transit
  if(olddaylight == daylight) olddaylight = !olddaylight;
  display.daysymbol();
} // end setup

void loop() {
  /* ------------------------------------------------- */
  /* Aquire time, every new minute read solar position */
  /* ------------------------------------------------- */
  rtc.refresh();
  if(rtc.second() == 0) {
    if(rtc.minute() == 0) {
      display.show_date();     // refresh date
      snprintf(binfile, sizeof(binfile), "20%d%02d%02d.BIN", 
                rtc.year(),rtc.month(),rtc.day());
      if(rtc.day() == 1) {
        snprintf(srsfile, sizeof(srsfile), "SRS-20%d.BIN", 
                rtc.year());
      }
      get_suntime(srsfile);
      display.show_rise_set(); // refresh sunrise/sunset
      display.show_transit();  // refresh transit
    }
    solar_position(binfile);
    display.daysymbol();
  }
  /* ------------------------------------------------- */
  /* Show Azimuth and sunrise/sunset on TFT            */
  /* ------------------------------------------------- */
  display.show_azimuth(azimuth);
  /* ------------------------------------------------- */
  /* Show Elevation on TFT, add leading + for daytime  */
  /* ------------------------------------------------- */
  display.show_elevation(zenith);
  /* ------------------------------------------------- */
  /* Show time on TFT                                  */
  /* ------------------------------------------------- */
  snprintf(lineStr, sizeof(lineStr), "Time: %02d:%02d:%02d",
  rtc.hour(),rtc.minute(),rtc.second());
  display.show_time(lineStr);
  /* ------------------------------------------------- */
  /* Aquire GPS sensor data                            */
  /* ------------------------------------------------- */
  // this hangs if there is no gps installed
  //if (GPS.available()) {
  //  latitude   = GPS.latitude();
  //  longitude  = GPS.longitude();
  // altitude   = GPS.altitude();
  //  speed      = GPS.speed();
  //  satellites = GPS.satellites();
  //}
  /* ------------------------------------------------- */
  /* Aquire compass sensor data                        */
  /* ------------------------------------------------- */
  compass.read();
  
  /* ------------------------------------------------- */
  /* If the sensor board orientation is unaligned, set */
  /* compass.heading((LSM303::vector<int>){0,1,0}) for */
  /* pointing along the Y-axis for example. Remove if  */
  /* the X-axis is the point of reference on a LSM303D */
  /* ------------------------------------------------- */
  /* Because magnetic north != real north, we adjust:  */
  /* Calculate magnetic declination and convergence    */
  /* to determine true North from magnetic North       */ 
  /* https://www.ngdc.noaa.gov/geomag/WMM/soft.shtml   */
  /* ------------------------------------------------- */
  if(compass.getDeviceType() == 3) heading = compass.heading() + mdecl;
  if(compass.getDeviceType() == 2) heading = compass.heading((LSM303::vector<int>){1,0,0}) + mdecl;
  if(heading < 0) heading = 360.0 + heading;
  /* ------------------------------------------------- */
  /* print North heading to TFT                        */
  /* ------------------------------------------------- */
  display.show_heading();
  /* ------------------------------------------------- */
  /* Convert heading angle to LED range value (0..48)  */   
  /* ------------------------------------------------- */
  hled = (int8_t)round((heading / 7.5) * 10 / 10.0);
  aled = (int8_t)round((azimuth / 7.5) * 10 / 10.0);
  rled = (int8_t)round((riseaz / 7.5) * 10 / 10.0);
  sled = (int8_t)round((setaz / 7.5) * 10 / 10.0);

  /* ------------------------------------------------- */
  /* If 48 is returned, it should roll over to 0       */   
  /* ------------------------------------------------- */
  if(hled > 47) hled = 0;
  if(aled > 47) aled = 0;
  if(rled > 47) rled = 0;
  if(sled > 47) sled = 0;
  /* ------------------------------------------------- */
  /* Because LED-1 is 90 degrees offset, we compensate */
  /* ------------------------------------------------- */
  hled = hled + 36; if(hled > 47) hled = hled - 48;
  /* ------------------------------------------------- */
  /* Reverse counting to keep the LED aligned to North */
  /* ------------------------------------------------- */
  hled = 48 - hled; if(hled > 47) hled = 0;
  /* ------------------------------------------------- */
  /* Remaining LED follow heading                      */
  /* ------------------------------------------------- */
  aled = hled + aled; if(aled > 47) aled = aled - 48;
  rled = hled + rled; if(rled > 47) rled = rled - 48;
  sled = hled + sled; if(sled > 47) sled = sled - 48;
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

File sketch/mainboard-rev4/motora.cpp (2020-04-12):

/* ---------------------------------------------------- *
 * Suntracker2 mainboard-rev4 motora.cpp 2019-10 @FM4DD *
 *                                                      *
 * This file has the functions to control the Azimuth   *
 * axis stepper motor.                                  *
 * ---------------------------------------------------- */
#include <Arduino.h>           // Arduino default library
#include "globals.h"           // global variable definitions

void AMotor::enable() {
  /* ------------------------------------------------- */
  /* Set azimuth motor control pins as output          */
  /* ------------------------------------------------- */
  pinMode(STEP1,OUTPUT); 
  pinMode(DIR1,OUTPUT);
  pinMode(ENA1,OUTPUT);
  pinMode(ESWI1,INPUT);
  digitalWrite(ENA1,HIGH); // Disable stepstick1
}

/* ---------------------------------------------------- */
/* demoturn demonstrates a 360 degree stepper turn      */
/* clockwise, and then returns back counterclockwise    */
/* Red LED will follow the indicator aligned with D1    */
/* ---------------------------------------------------- */
void AMotor::demoturn(uint8_t count) {
  int mled;               /* To move one red LED clockwise  */
  int oldmled;            /* To turn off the previous LED   */
  mcp1.writeGPIOAB(0x00); /* Turn off all red LED 1..16     */
  mcp2.writeGPIOAB(0x00); /* Turn off all red LED 17..32    */
  mcp3.writeGPIOAB(0x00); /* Turn off all red LED 33..48    */
  digitalWrite(ENA1,LOW); /* Enable stepstick1 motor driver */
  for(uint8_t turn = 0; turn < count; turn++) {
    digitalWrite(DIR1,HIGH); /* clockwise motor direction    */
    for(float x = 0; x < 800; x++) { /* 1600 steps = 1 turn */
      digitalWrite(STEP1,HIGH); 
      delayMicroseconds(SLOW); 
      digitalWrite(STEP1,LOW); 
      delayMicroseconds(SLOW);
      mled = (int) round(x / 17); /* 1600/47=34, round to int */ 
      if (mled != oldmled) {
        if(oldmled < 16) mcp1.digitalWrite(oldmled, LOW);
        else if(oldmled < 32) mcp2.digitalWrite((oldmled-16), LOW);
        else if(oldmled < 48) mcp3.digitalWrite((oldmled-32), LOW);
        if(mled > 31) mcp3.digitalWrite((mled-32), HIGH);
        else if(mled > 15) mcp2.digitalWrite((mled-16), HIGH);
        else if(mled < 16) mcp1.digitalWrite(mled, HIGH);
        oldmled = mled;
      }
    }
    mcp1.digitalWrite(0, HIGH); /* Last value is 48, turns 1 */
    mcp3.digitalWrite(15, LOW);  /* and delete previous LED  */
    
    delay(1000);                /* Wait for one second delay */
    oldmled = 0;                /* Reset the old LED value   */
    digitalWrite(DIR1 ,LOW);     /* Set dir counterclockwise */
    for(double x = 799; x >= 0; x--) { /* 1599..0 steps 1 turn */
      digitalWrite(STEP1, HIGH);
      delayMicroseconds(SLOW);
      digitalWrite(STEP1, LOW);
      delayMicroseconds(SLOW);
      mled = round(x / 17); /* 1600/48=33.3, round to int  */
      if (mled != oldmled) {
        if(oldmled < 16) mcp1.digitalWrite(oldmled, LOW);
        else if(oldmled < 32) mcp2.digitalWrite((oldmled-16), LOW);
        else if(oldmled < 48) mcp3.digitalWrite((oldmled-32), LOW);
        if(mled > 31) mcp3.digitalWrite((mled-32), HIGH);
        else if(mled > 15) mcp2.digitalWrite((mled-16), HIGH);
        else if(mled < 16) mcp1.digitalWrite(mled, HIGH);
        oldmled = mled;
      }
    }
    mcp1.digitalWrite(0, HIGH); /* Turn the last LED 2 to 1  */
    mcp3.digitalWrite(15, LOW);  /* and delete previous LED  */
    delay(1000);                /* Wait for one second delay */
  }
  digitalWrite(ENA1, HIGH); /* Disable stepstick1 motordriver */
  mcp1.writeGPIOAB(0x00);   /* Turn off all red LED 1..16     */
  mcp2.writeGPIOAB(0x00);   /* Turn off all red LED 17..32    */
  mcp3.writeGPIOAB(0x00);   /* Turn off all red LED 17..32    */
}

/* ---------------------------------------------------- */
/* oneturn turns 360 degrees, argument gives direction  */
/* ---------------------------------------------------- */
void AMotor::oneturn(boolean direction, int speed) {
  digitalWrite(ENA1,LOW); /* Enable stepstick1 motor driver */
  digitalWrite(DIR1,direction); /* HIGH=clockwise, LOW=CCW  */
  for(float x = 0; x < 800; x++) { /* 1600 steps = 1turn */
    digitalWrite(STEP1,HIGH); 
    delayMicroseconds(speed); 
    digitalWrite(STEP1,LOW); 
    delayMicroseconds(speed);
  }
  digitalWrite(ENA1, HIGH); /* Disable stepstick1 motordriver */
}

/* ---------------------------------------------------- */
/* adjust moves from the current position towards the   */
/* target position in one go. position range 0..1600    */
/* ---------------------------------------------------- */
void AMotor::adjust(uint16_t target, int speed) {
  uint16_t steps = 0;
  m1move = true;
  digitalWrite(ENA1,LOW); /* Enable stepstick1 motor driver */
  if(m1cpos < m1tpos) {
    if(abs(m1cpos - m1tpos) < 400) {
      digitalWrite(DIR1,HIGH); /* run clockwise motor direction */
      steps = m1tpos - m1cpos; /* get required steps to target  */
    }
    else {                    /* the other way around is shorter */
      digitalWrite(DIR1,LOW); /* move counterclockwise direction */
      steps = 400 - m1tpos + m1cpos;
    }
  }
  else {
    if((m1cpos - m1tpos) < 400) {
      digitalWrite(DIR1,LOW); /* counterclockwise  direction  */
      steps = m1cpos - m1tpos;
    }
    else {                     /* the other way around is shorter */
      digitalWrite(DIR1,HIGH); /* run clockwise motor direction   */
      steps = 800 - m1cpos + m1tpos;      
    }
  }
  for(int x = 0; x < steps; x++) {
      digitalWrite(STEP1,HIGH);
      delayMicroseconds(speed);
      digitalWrite(STEP1,LOW); 
      delayMicroseconds(speed);
  }
  //digitalWrite(ENA1,HIGH); /* Disable stepstick1 motordriver */
  m1move = false;
  m1cpos = m1tpos;
}

/* ---------------------------------------------------- */
/* poweron enables the stepstick controller and sets    */
/* the motor move variabe m1move to 'true'.             */
/* ---------------------------------------------------- */
void AMotor::poweron() {
  if(digitalRead(ENA1) == HIGH) {
    digitalWrite(ENA1,LOW); /* Enable stepstick1 motor driver */
    m1move = true;
  }
}

/* ---------------------------------------------------- */
/* poweroff enables the stepstick controller and sets   */
/* the motor move variabe m1move to 'false'.            */
/* ---------------------------------------------------- */
void AMotor::poweroff() {
  if(digitalRead(ENA1) == LOW) {
    digitalWrite(ENA1,HIGH); /* Disable stepstick1 motor driver */
    m1move = false;
  }
}
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

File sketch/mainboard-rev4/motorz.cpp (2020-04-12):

/* ---------------------------------------------------- *
 * Suntracker2 mainboard-rev4 motorz.cpp 2019-10 @FM4DD *
 *                                                      *
 * This file has the functions to control the Zenith    *
 * axis stepper motor.                                  *
 * ---------------------------------------------------- */
#include <Arduino.h>           // Arduino default library
#include "globals.h"           // global variable definitions

void ZMotor::enable() {
  /* ------------------------------------------------- */
  /* Set zenith motor control pins as output           */
  /* ------------------------------------------------- */
  pinMode(STEP2,OUTPUT); 
  pinMode(DIR2,OUTPUT);
  pinMode(ENA2,OUTPUT);
  pinMode(ESWI2,INPUT);
  digitalWrite(ENA2,HIGH); // Disable stepstick2
}

/* ---------------------------------------------------- */
/* poweron enables the stepstick controller and sets    */
/* the motor move variabe m1move to 'true'.             */
/* ---------------------------------------------------- */
void ZMotor::poweron() {
  if(digitalRead(ENA2) == HIGH) {
    digitalWrite(ENA2,LOW); /* Enable stepstick2 motor driver */
    m2move = true;
  }
}

/* ---------------------------------------------------- */
/* poweroff enables the stepstick controller and sets   */
/* the motor move variabe m1move to 'false'.            */
/* ---------------------------------------------------- */
void ZMotor::poweroff() {
  if(digitalRead(ENA2) == LOW) {
    digitalWrite(ENA2,HIGH); /* Disable stepstick2 motor driver */
    m2move = false;
  }
}

/* ---------------------------------------------------- */
/* demoturn demonstrates a 90 degree stepper turn       */
/* counterclockwise, and then returns back clockwise    */
/* Red LED will follow the indicator aligned with D1    */
/* ---------------------------------------------------- */
void ZMotor::demoturn(uint8_t count) {
  int mled = 0;           /* To move one red LED clockwise  */
  int oldmled = 41;       /* To turn off the previous LED   */
  mcp6.writeGPIOAB(0x00); /* Turn off all green LED 1..16   */
  mcp7.writeGPIOAB(0x00); /* Turn off all red LED 1..16     */
  digitalWrite(ENA2,LOW); /* Enable stepstick2 motor driver */
  for(uint8_t turn = 0; turn < count; turn++) {
    digitalWrite(DIR2,HIGH); /* clockwise motor direction    */
    for(int x = 0; x < 640; x++) { /* 0..639 = 90 degrees    */
      digitalWrite(STEP2,HIGH); 
      delayMicroseconds(SLOW); 
      digitalWrite(STEP2,LOW); 
      delayMicroseconds(SLOW);
      mled = x / 40; /* 800/16=50, round to int */ 
      if (mled != oldmled) {
        mcp7.digitalWrite(oldmled, LOW);
        mcp7.digitalWrite(mled, HIGH);
        oldmled = mled;
      }
    }
    digitalWrite(DIR2 ,LOW);     /* Set dir counterclockwise */
    delay(1000);                /* Wait for one second delay */
    for(int x = 639; x >= 0; x--) {  /* 639 ..0 = 90 degrees */
      digitalWrite(STEP2, HIGH);
      delayMicroseconds(SLOW);
      digitalWrite(STEP2, LOW);
      delayMicroseconds(SLOW);
      mled = x / 40; /* 640/16=40, round to int  */
      if (mled != oldmled) {
        mcp7.digitalWrite(oldmled, LOW);
        mcp7.digitalWrite(mled, HIGH);
        oldmled = mled;
      }
    }
    delay(1000);                /* Wait for one second delay */
  }
  digitalWrite(ENA2, HIGH); /* Disable stepstick1 motordriver */
  mcp7.writeGPIOAB(0x00);   /* Turn off all red LED 1..16     */
}
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

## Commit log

2019-11-17 s2r4 init
    [20190922 Suntracker2r4 block diagram.dxf, 20191012 suntracker2r4-mainboard-bottom-v1.0.dxf, 20191012 suntracker2r4-mainboard-stands-v1.0.dxf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]
2019-11-17 s2r4 add assembly
2019-11-30 add screen image, fix stepper test output
    [globals.cpp, mainboard-rev4.ino]
2020-01-28 zenith motor 1st tests
2020-04-12 Add XBee communication code
    [20190922 Suntracker2r4 block diagram.dxf, 20191012 suntracker2r4-mainboard-bottom-v1.0.dxf, 20191012 suntracker2r4-mainboard-stands-v1.0.dxf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]
